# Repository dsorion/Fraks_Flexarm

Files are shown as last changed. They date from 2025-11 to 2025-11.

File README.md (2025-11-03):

# FRAKS Flexarm

Fraks Flexarm

### Free Range Arm Kinematics System

The Fraks Flexarm is a tool-balancing arm designed to keep the attached tool parallel throughout its movement. It was created to hold soldering irons to install heat set inserts into 3D printed parts.

It has a large working area for its size, and has quick release tool holders that are held in place with magnets.

Thanks to Zack Freedman for making Gridfinity an open source project, I have included Gridfinity storage into the base. You can read more about Gridfinity at <https://gridfinity.xyz/>

Fraks Animation

___

# What do I need?

* You will also need either pocket screws or a wood working fence clamp to secure the base to your work surface.

* 4 pieces of 1515 extrusion, all cut to the same length and tapped on either end. I have tested this with 200mm and 270mm lengths.

* 10x1x60mm extension springs, these seem to work well for 200-300mm builds. You can adjust the tension rate by moving the spring posts along the 1515 extrusion.

* 10x100mm dowel pin and a 10x14x30mm brass Bushing

* M10 washer, a 25mm diameter is listed, but any diameter and thickness washer will work.

* M5x30 FHCS are recommended, but BHCS are also supported. The springs will touch button heads slightly, but will not affect performance from testing.

* You will need a Soldering iron with a heatset insert adapter. I personally recommend either the Pinecil or TS101 Soldering Irons along with the adapter set from CNC Kitchen.

| **Current Supported Irons:** | |
|---|---|
| **Pinecil** with CNC Kitchen TS100&TS101 Adapter Set |Pinecil |
| **TS101** with CNC Kitchen TS100&TS101 Adapter Set |PTS101 |
| Imported adjustable solder iron (Generic) |China_Soldering_iron |

___

## BOM

| Part Description | Quantity | |
|---|---|---|
| 1515 Extrusion 200-300mm (All the same length) | 4 |1515_Extrusion |
| 10mm OD x 1mm Wire Gauge x 60mm Long Extension Springs | 4 |10X1X60_Spring |
| 10mm x 100mm long Pin | 1 |Pin |
| 10mm ID x 14mm OD x 30mm Length Brass Bushing | 1 |10x14x30_Bushing |
| 10mmx24mm Washer | 1 |10x24x1_Shim |
| M3x8 FHCS | 16 |M3x8_FHCS |
| M3x8 SHCS | 10 |M3x8_SHCS |
| M3x12 BHCS | 4 |M3x12_BHCS |
| M3x20 BHCS | 4 |M3x20_BHCS |
| M5x30 FHCS (Or BHCS) | 8 |M5x30_BHCS |
| M3 Heatset Inserts (5mm OD x 4mm Length) | 10 |M3 Heatset |
| M3 Hex Nuts | 20 |M3_Hex_Nut |
| M5 Washers/Shims (10x1) | 16 |M5x10x1_Shim |
| 6x3 Magnets | 6 |6x3_Magnet |
| 6x2 Magnets (For Gridfinity Base) | 24 |6x2_Magnet |
| 1-1/4 #8 Pocket screws (For screwing base to table) | 4 |Pocket_Screw |
| Table Saw Fence Clamp (For clamping to table) | 1 |Fence_Clamp |

___

## Amazon links

[Fence Clamps](https://www.amazon.com/gp/product/B07CJHZ7QL/ref=ox_sc_act_title_2?smid=ATVPDKIKX0DER&th=1)

[10x1x60 Springs](https://www.amazon.com/gp/product/B0CJFFL9MW)

[10x14x30 Bushing](https://www.amazon.com/gp/product/B09QYQS7RX)

<br>

## Vendor Kits

[DLL-PDF](https://dllpdf.com/fraks-flexarm) - Has extrusion kits and a M3/M5 Screw only hardware option. They offer custom powder-coating, and will cut the extrusions to any length you want.

[Dremc](https://store.dremc.com.au/en-us/products/fraks-flexarm-kit) - Has a complete hardware kit, and sells extrusions in various lengths.

[Fabreeko](https://www.fabreeko.com/products/fraks-flexarm-heat-insert-press-kits-by-turtle-crawler)   -
 Offers complete kits in 3 sizes, 300mm, 350mm, and 400mm. A portion of all sales from the Fabreeko listing are donated to me.

[KB-3D](https://kb-3d.com/store/tools-equipment/3474-fraks-flexarm-system-heat-set-insert-tool-configurator.html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) - Offers customizable kits that let you pick and choose exactly what you need. This is great if you already have a good assortment of hardware. They also have the TS101 Iron and CNC Kitchen tip set. This is an affiliate link, and using this link will give me a small kickback of the total order.

___

# Print Settings

* 0.2mm layer heights

* 0.4mm Line Width

* 4-5 walls

* 4-5 top and bottom layers

* 40% infill

* ABS and ASA have been tested

# Assembly Tips

___

* The center arms use a pair of magnets to pull the arms together when parked. Build 2 arms with magnets that that attract to each other.

Arm_Hardware_01

* Build the other 2 arms like the image bellow, with the spring standoffs placed 90mm from one end. You can adjust these later.

Arm_Hardware_01

___

# Change Log

November 2nd, 2025:

* Increased the thickness of the guard by 0.8mm, this should solve the issue that some users have had with breaking the guard.

* Doublde the BOM Count for the 6x2 Magnets used for Gridfinity, as to include enough for the trays as well as the base.

* Added a short readme about the 695 Bearing mod under the stl directory for them.

___

## *Refer to cad for further assembly help*

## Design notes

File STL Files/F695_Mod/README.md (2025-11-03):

# Bearing Mod

This was from the very first few versions of Fraks that I built, and I found that it worked better with a bit of friction.

But I decided to still share the files, it does have a smoother motion but cannot hold its position, so must be parked after each use.

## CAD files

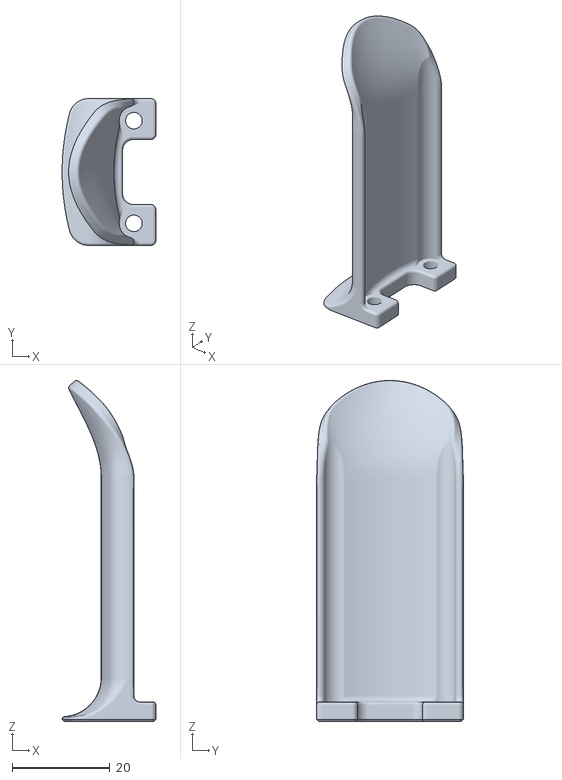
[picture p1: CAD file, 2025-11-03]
STL Files/Front_bracket_Guard_Long.stl
19.2 x 30.0 x 69.7

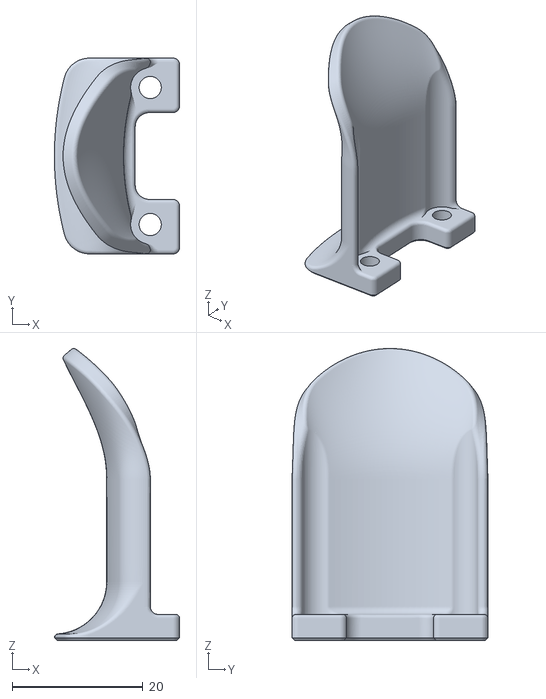
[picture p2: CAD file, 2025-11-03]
STL Files/Front_bracket_Guard_Medium.stl
19.2 x 30.0 x 44.7
